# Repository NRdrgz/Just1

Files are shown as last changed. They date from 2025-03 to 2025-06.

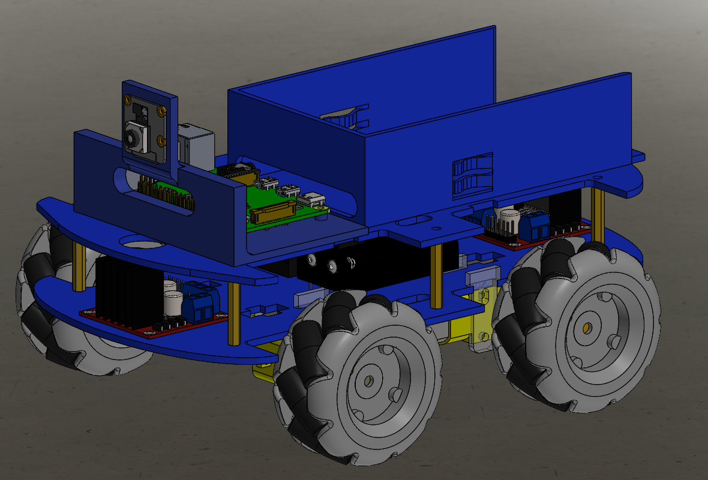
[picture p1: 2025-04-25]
Bot/Hardware/Just1Model.png

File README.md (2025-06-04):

# Just1 - An Open-Source Mecanum Wheel Robot

Just1 is an open-source robotics platform designed for learning, experimentation, and fun! Built around a Raspberry Pi and equipped with mecanum wheels, this robot offers both manual control and autonomous navigation capabilities.

## Project Goals

Just1 was created with several objectives in mind:
- Provide a fun and engaging robotics platform
- Develop practical robotics and programming skills
- Share knowledge and encourage others to build their own robots
- Create an accessible platform for learning and experimentation

## Workspace Organization

### Hardware
Located in `/Bot/Hardware`:
- Bill of Materials (BoM)
- SolidWorks design files
- Assembly instructions and wiring diagrams

### Software
Located in `/Bot/Software`:
- ROS2 packages
- Installation guides
- Manual control documentation

## Current Features

- Complete hardware design with BoM and SolidWorks files
- Comprehensive software documentation for Raspberry Pi setup
- Manual control using Nintendo Controller
- Real-time camera feed accessible via homemade web interface or through Foxglove

## Features in Progress

- Autonomous navigation using ROS2 VSLAM (RTAB Map)
- Add documentation on Camera feedback through websocket

## Short-term To-Do List

- Create detailed README for Hardware folder
- Add assembly and wiring documentation
- Add control and camera feedback on phone
- Use Foxglove CompressedVideo instead of CompressedImage for Camera feedback

## Long-term Goals and Potential Improvements

- Add a Docker Image for easier and faster deployment
- Perform Navigation through Neural Network architecture instead of VSLAM 
- Replace AA batteries with voltage booster for simplified power management
- Integrate LIDAR system, IMU and/or wheel encoders for advanced navigation and experimentation
- Integrate memory / latency profilers to optimize processes and detect memory leaks

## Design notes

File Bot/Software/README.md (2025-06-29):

# Just1 Software

This is a ROS2-based control system for a four-wheeled robot with joystick control.

## References for external ROS packages
- Camera ROS: https://index.ros.org/p/camera_ros/
- Foxglove Bridge: https://github.com/foxglove/ros-foxglove-bridge
- RTAB-Map: https://github.com/introlab/rtabmap_ros

## Installation

1. Install Ubuntu Server 24.04 on your Pi <br>
See `Reads/How_to_Install_Ubuntu_on_Pi.md` <br>
Once you are connected through SSH to your Pi, continue: <br>

2. Install ROS2 on your Pi <br>
See `Reads/How_to_Install_ROS2_on_Pi.md` <br>
We are voluntarily not using a virtual environment because it creates issues with the Camera and with ROS2 <br>

3. Install git and clone this repository on your Pi <br>
```bash
sudo apt install git -y
git clone https://github.com/NRdrgz/Just1.git
cd Just1/Bot/Software
```

4. Install Dependencies: <br>
```bash
sudo apt install python3-pip python3-gpiozero python3-pygame libcap-dev ninja-build libyaml-dev python3-yaml python3-ply python3-jinja2 meson libdrm ros-jazzy-foxglove-bridge python3-smbus i2c-tools ros-jazzy-rtabmap-ros ros-jazzy-imu-filter-madgwick ros-jazzy-navigation2 ros-jazzy-nav2-bringup
pip install --break-system-packages -r requirements.txt
```
5. Build libcamera from source <br>
As libcamera is not available on Ubuntu Server 24.04 we need to install it from the source
```bash
cd ~
git clone https://git.libcamera.org/libcamera/libcamera.git
cd libcamera
meson setup build
sudo ninja -C build install
```
Add the directory to Python search path
```bash
echo 'export PYTHONPATH=/usr/local/lib/aarch64-linux-gnu/python3.12/site-packages:$PYTHONPATH' >> ~/.bashrc
source ~/.bashrc
```

And we also have to build from source pykms
```bash
cd ~
git clone https://github.com/tomba/kmsxx.git
cd kmsxx
meson setup build
sudo ninja -C build install
```
```bash
echo 'export LD_LIBRARY_PATH=/usr/local/lib/aarch64-linux-gnu:$LD_LIBRARY_PATH' >> ~/.bashrc
source ~/.bashrc
```

6. Connect a Nintendo Lic Pro Controller if you have one <br>
See `Reads/How_to_Connect_Nintendo_Pro_Controller.md` <br>

7. Build the ROS2 packages: <br>
```bash
cd ~/Just1/Bot/Software
colcon build --symlink-install
```

To build a single package you can do <br>
```bash
colcon build --packages-select <package_name> --symlink-install
```

8. Source the workspace: <br>
```bash
source install/setup.bash
```

## Usage in Manual
At this point you can control the robot manually. <br>
To start the manual control system: <br>

```bash
ros2 launch just1_bringup just1.launch.py mode:=manual
```

## Get the Video feed
To see the video captured from the Camera, you can either
- Use Foxglove (preferred) <br>
The foxglove_bridge_node used in just1_bringup is used to select the relevant topics to whitelist to Foxglove <br>
You can then visualize Camera data in a Foxglove UI <br>

- Use the homemade websocket:
Activate the camera_web_socket node in just1.launch.py <br>
Navigate to the Web page in src/just1_camera/web/Webpage.html <br>
Make sure to change the PI ip address in the Webpage <br>

## Continue installation for Autonomous mode

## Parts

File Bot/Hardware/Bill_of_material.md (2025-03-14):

# Bill of Material

This are the components used to build Junior.

| Item | Description | Link (as of March 2025) | Total Price (as of March 2025) | Why |
| --- | --- | --- | --- | --- |
| Control Unit | Raspberry Pi v4 8Gb | [Link](https://www.adafruit.com/product/4564?src=raspberrypi) | $83 | 8Gb to have enough memory for AI vision. The Raspberry Pi v5 is great by 5A power supply is hard to find |
| Micro SD card | 16GB Micro SD Card | [Link](https://www.amazon.com/Micro-Adapter-Memory-Tablet-Camera/dp/B0DBLWVSM8) | $7 | Used to install OS on the Pi |
| Wheels + Motors | 4 x 60mm Mecanum Wheels + 4 TT Motors | [Link](https://www.amazon.com/DWWTKL-Mecanum-Omnidirectional-Educational-Accessory/dp/B0CBJJM1KQ) | $16 | Great combo of wheels and TT motors with proper adapters to connect the wheels and motors |
| Motor Drivers | 2 x L298N | [Link](https://www.amazon.com/Controller-H-Bridge-Stepper-Control-Mega2560/dp/B0DPPWFZ1C) | $14 | Cheap with Mosfet but good enough |
| Sensors | Camera Module 3 | [Link](https://www.adafruit.com/product/5657?src=raspberrypi) | $25 |  |
| Pi Power Unit | Power bank for Raspberry Pi | [Link](https://www.amazon.com/Portable-36800mAh-Tri-Outport-External-Compatible/dp/B0936GZ7H3) | $25 | Power bank has a 5V 3A USB C output good for Pi |
| Motors Power Unit | 6 AA batteries holder for motors  | [Link](https://www.amazon.com/LAMPVPATH-Battery-Holder-Bundle-Arduino/dp/B07BNN9PDF) | $7 | Provide 9V to the Motor Drivers |
| Chassis | See 3D models |  | $0 if you find a Robotic club |  |
| **Total** |  |  | **$177** |  |

Here are a bunch of useful screws and wires.
| Item | Link (as of March 2025) | Total Price (as of March 2025) | Why |
| --- | --- | --- | --- |
| Female Female Jumper Wires | [Link](https://www.amazon.com/dp/B09FP5PW45?ref=ppx_yo2ov_dt_b_fed_asin_title&th=1) | $7 | Connect Pi to Motor Driver | 
| Various 2.5 Screws | [Link](https://www.amazon.com/dp/B0CRRCYZHS?ref=ppx_yo2ov_dt_b_fed_asin_title&th=1) | $10 | Screw Pi or Motor drivers | 
| Hex Pylons | [Link](https://www.amazon.com/dp/B01EYQ1TGE?ref=ppx_yo2ov_dt_b_fed_asin_title&th=1) | $10 | Separate both layers of 3D model |

You`ll also need standard wires, soldering iron.

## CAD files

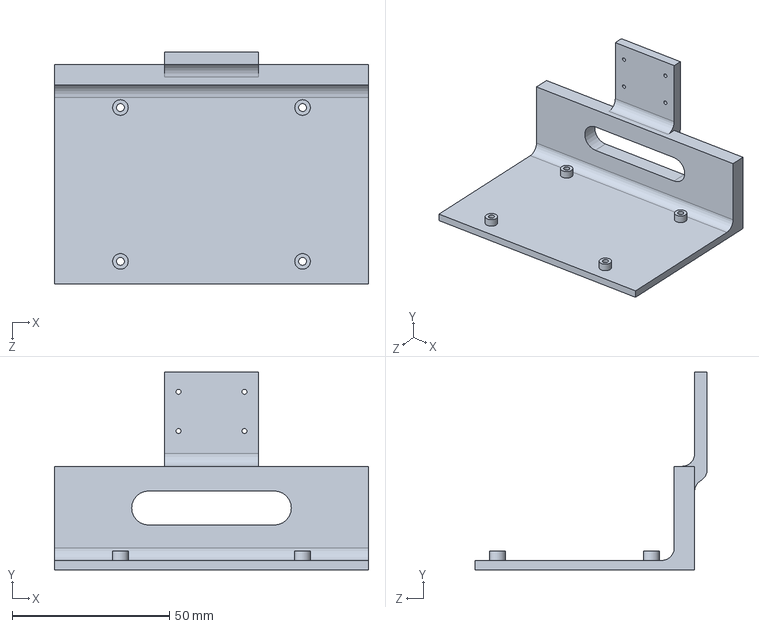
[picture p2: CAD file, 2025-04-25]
Bot/Hardware/Solidworks/Parts/Raspberry Holder.SLDPRT
100.0 x 63.0 x 74.0 mm

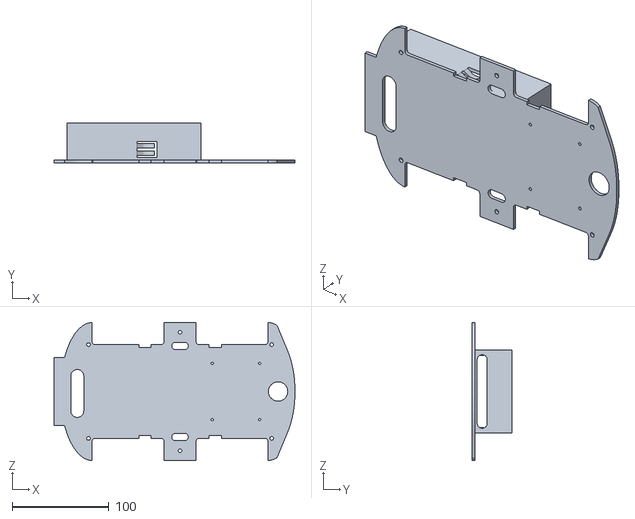
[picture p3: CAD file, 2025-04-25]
Bot/Hardware/Solidworks/ToPrint/Car chassis - top.STL
248.8 x 40.8 x 142.5

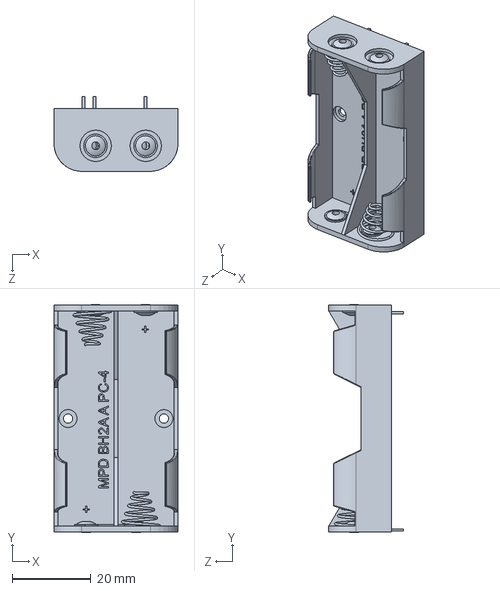
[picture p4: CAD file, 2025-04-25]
Bot/Hardware/Solidworks/Parts/2x AA Battery Pack.SLDPRT
31.5 x 58.0 x 19.0 mm

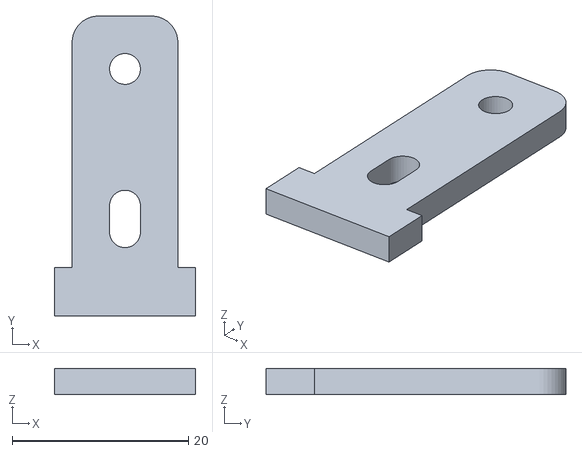
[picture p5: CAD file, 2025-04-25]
Bot/Hardware/Solidworks/ToPrint/Holder Motor.STL
16.0 x 34.0 x 3.00

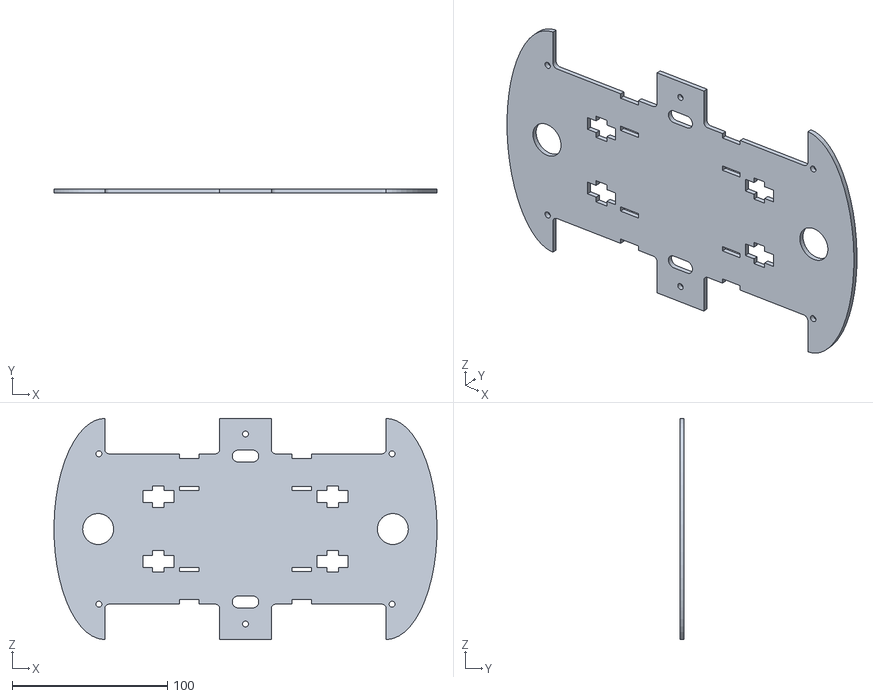
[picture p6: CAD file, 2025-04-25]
Bot/Hardware/Solidworks/ToPrint/Car chassis bottom.STL
247.0 x 2.85 x 142.5

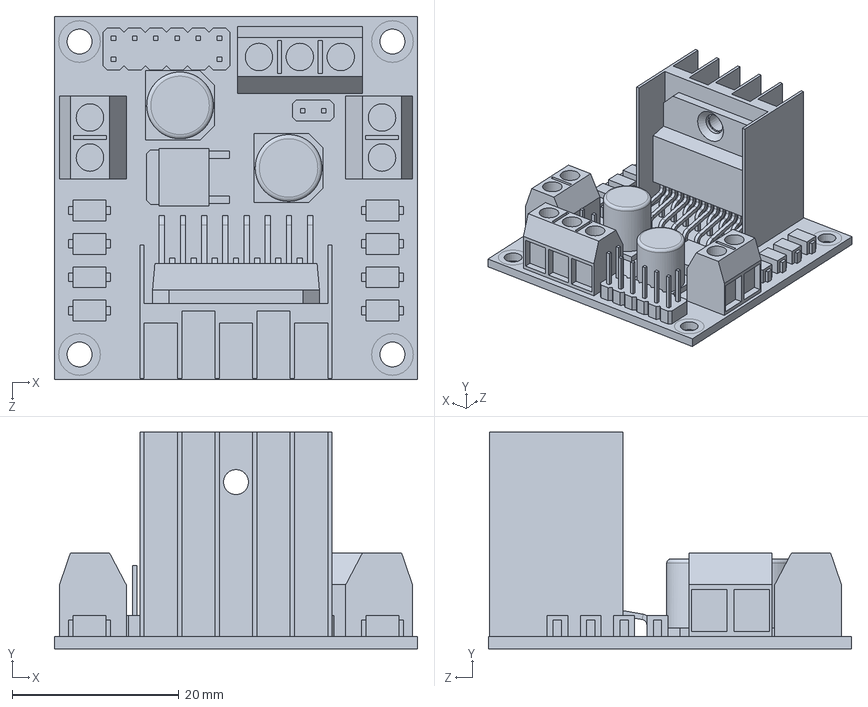
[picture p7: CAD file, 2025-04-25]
Bot/Hardware/Solidworks/Parts/L298N.SLDPRT
43.5 x 26.0 x 43.5 mm

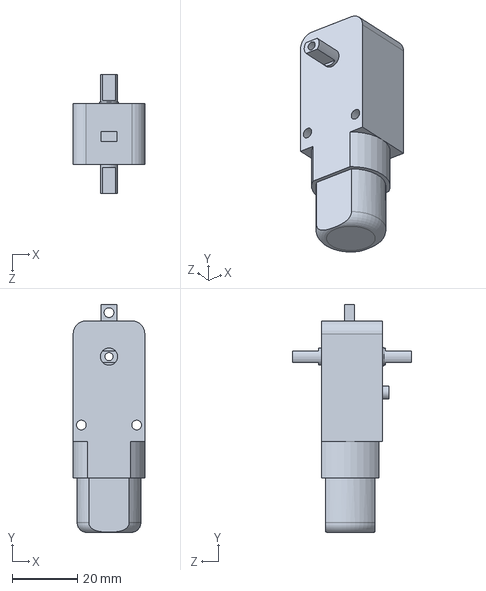
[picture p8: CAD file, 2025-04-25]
Bot/Hardware/Solidworks/Parts/TT motor.SLDPRT
22.0 x 70.0 x 36.6 mm

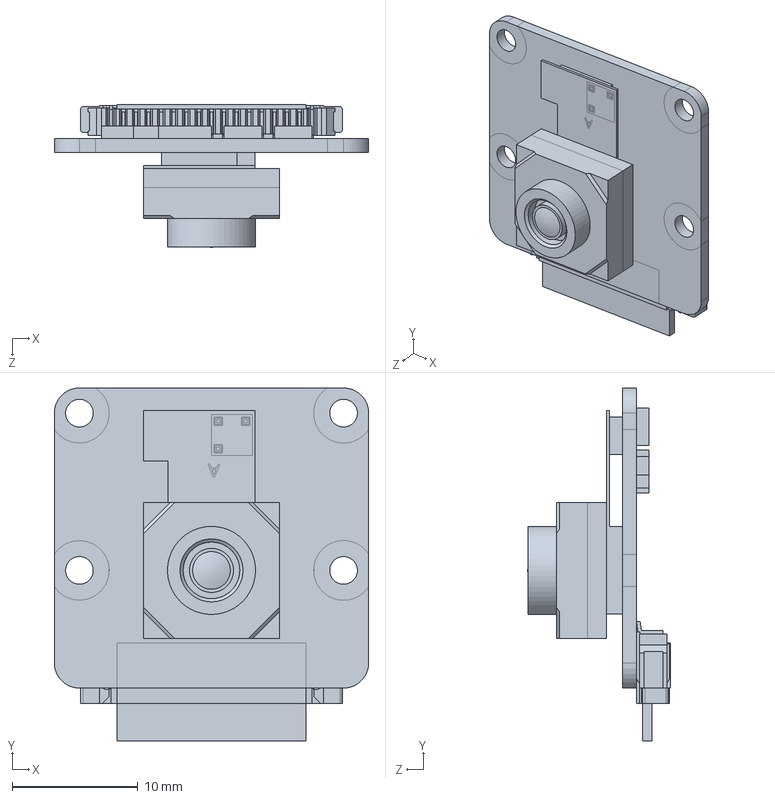
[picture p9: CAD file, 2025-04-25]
Bot/Hardware/Solidworks/Parts/Camera Moudule 3 v8.SLDPRT
25.0 x 28.1 x 11.3 mm

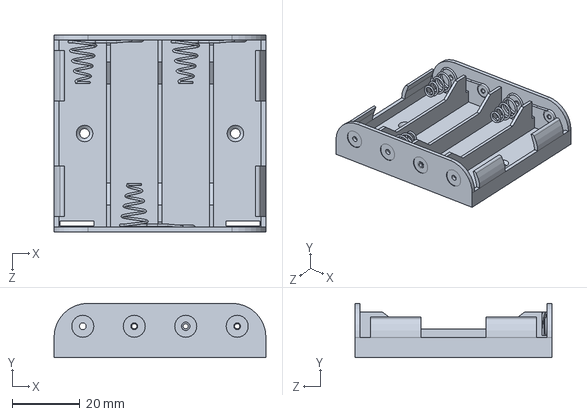
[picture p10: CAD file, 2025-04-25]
Bot/Hardware/Solidworks/Parts/4x AA Battery Pack.SLDPRT
62.4 x 16.0 x 58.0 mm

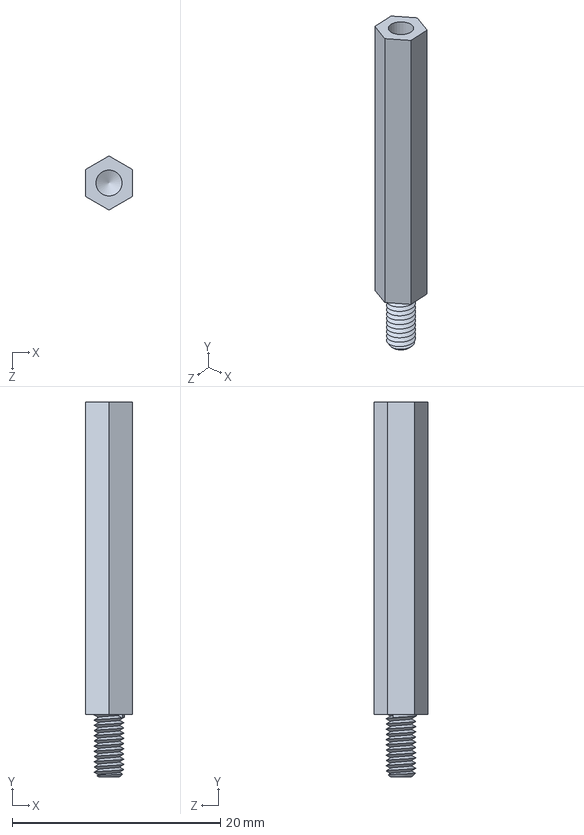
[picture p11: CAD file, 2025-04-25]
Bot/Hardware/Solidworks/Parts/Pillar Hex.SLDPRT
4.50 x 36.0 x 5.20 mm

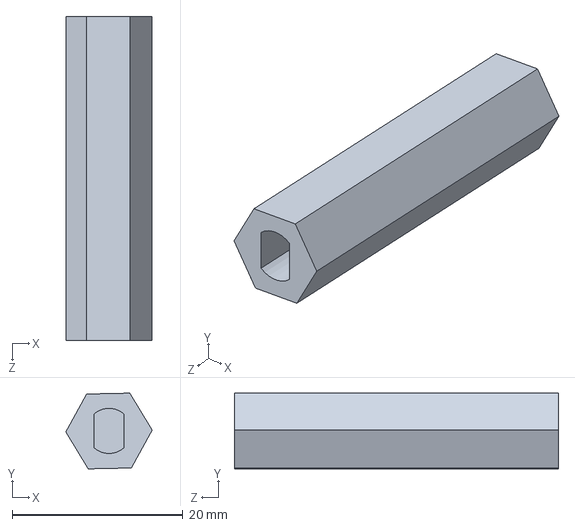
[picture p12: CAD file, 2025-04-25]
Bot/Hardware/Solidworks/Parts/Coupling Adapter.SLDPRT
10.1 x 8.89 x 38.0 mm

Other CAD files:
Bot/Hardware/Solidworks/Parts/Holder Motor.SLDPRT
Bot/Hardware/Solidworks/ToPrint/Raspberry Holder.STL
Bot/Hardware/Solidworks/Parts/Car chassis - top.SLDPRT
Bot/Hardware/Solidworks/Parts/Car chassis bottom.SLDPRT

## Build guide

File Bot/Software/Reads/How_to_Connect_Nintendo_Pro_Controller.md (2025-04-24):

# Connect to the Nintendo Lic Pro Controller
To connect to the Lic Pro Controller from the Raspberry Pi <br>
First make sure Pi has bluetooth enabled <br>
```bash
sudo apt install bluetooth bluez bluez-tools rfkill -y
sudo systemctl enable bluetooth
sudo systemctl start bluetooth
```

Put controller in pairing mode  <br>
Then <br>
```bash
bluetoothctl
power on
agent on
default-agent
scan on
```

You'll see something like  <br>
[NEW] Device XX:XX:XX:XX:XX:XX Lic Pro Controller <br>

```bash
pair XX:XX:XX:XX:XX:XX
trust XX:XX:XX:XX:XX:XX
connect XX:XX:XX:XX:XX:XX
```

Then <br>
```bash
exit
```

You can verify if it worked by using joystick <br>
```bash
sudo apt install joystick
jstest /dev/input/js0
```

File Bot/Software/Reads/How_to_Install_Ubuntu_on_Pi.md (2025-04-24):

# Install Ubuntu on Raspberry Pi 
## Step 1: Download Ubuntu Image

1. Go to the [Ubuntu Raspberry Pi page](https://ubuntu.com/raspberry-pi).
2. Download your preferred version (e.g., Ubuntu Server 24.04 LTS). Make sure to install Ubuntu Server instead of Ubuntu Desktop if you want to avoid plugging keyboard and mouse on the Pi.

---

## Step 2: Flash the Image to microSD

1. Download and install the [Raspberry Pi Imager](https://www.raspberrypi.com/software/).
2. Launch the Imager and:
   - **Choose OS**: Select “Other general-purpose OS > Ubuntu”
   - **Choose Storage**: Select your microSD card
   - **Customize before writing**:
     - You should have a popup offering you to input custom settings
     - Enable **Set hostname** (e.g., `raspberrypi.local`). This will allow to connect to it without IP address
     - Enable and set **SSH** (e.g., username `your-username`, password `your-password`)
     - Enable and configure **Wi-Fi**:
       - SSID: `your-network-name`
       - Password: `your-password`
       - Wi-Fi country: `US` (or your 2-letter country code)

3. Click **Save**, then **Write** to flash the image.

---

## Step 3: First Boot

1. Insert the microSD into your Raspberry Pi.
2. Power it on.

The Pi will:
- Automatically connect to the Wi-Fi
- Enable SSH access
- Be ready for headless setup

Wait for 5-10 min for the installation to complete

---

## Step 4: Connect via SSH

Once the Pi is online, open a terminal on your computer and connect using:

```bash
ssh your-username@raspberrypi
```

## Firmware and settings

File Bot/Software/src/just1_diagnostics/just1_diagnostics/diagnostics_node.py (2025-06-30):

import rclpy
from rclpy.node import Node
import time
from just1_motors.utils_motors import (
    setup,
    stop_all,
    test_wheel,
    cleanup,
    control_wheel,
)
from sensor_msgs.msg import Joy


class DiagnosticsNode(Node):
    def __init__(self):
        super().__init__("diagnostics_node")
        self.get_logger().info("Diagnostics Node initialized")

        # Declare parameters
        self.declare_parameter("test_wheel", "")
        self.declare_parameter("test_movement", "")
        self.declare_parameter("test_joystick", False)
        self.declare_parameter("speed", 50)

        # Initialize GPIO and motors
        setup()

        # Create subscriber for joystick
        self.joystick_subscriber = self.create_subscription(
            Joy, "joy", self.joystick_callback, 10
        )
        self.joystick_data = None

        # Run diagnostics based on parameters
        self.run_diagnostics()

    def joystick_callback(self, msg):
        """Callback for joystick messages"""
        self.joystick_data = msg

    def run_diagnostics(self):
        """Run diagnostics based on parameters"""
        test_wheel = self.get_parameter("test_wheel").get_parameter_value().string_value
        test_movement = (
            self.get_parameter("test_movement").get_parameter_value().string_value
        )
        test_joystick = (
            self.get_parameter("test_joystick").get_parameter_value().bool_value
        )
        speed = self.get_parameter("speed").get_parameter_value().integer_value

        if test_wheel:
            self.test_wheel(test_wheel)
            self.cleanup_and_shutdown()
        elif test_movement:
            self.test_movement(test_movement, speed)
            self.cleanup_and_shutdown()
        elif test_joystick:
            self.test_joystick()
        else:
            self.get_logger().error("No valid test option specified")
            self.cleanup_and_shutdown()

    def cleanup_and_shutdown(self):
        """Cleanup and shutdown the node"""
        cleanup()
        self.get_logger().info("Diagnostics completed")
        rclpy.shutdown()

    def test_joystick(self):
        """Display joystick values"""
        print("\nJoystick Test Mode")
        print("Press Ctrl+C to exit")
        print("Waiting for joystick data...")

        # Create a timer to periodically check joystick data
        self.timer = self.create_timer(0.1, self.print_joystick_data)

    def print_joystick_data(self):
        """Print joystick data periodically"""
        if self.joystick_data is not None:
            print("\n" + "=" * 50)
            print("Joystick Data:")
            print(f"Axes: {[f'{x:.2f}' for x in self.joystick_data.axes]}")
            print(f"Buttons: {self.joystick_data.buttons}")
            print("=" * 50)

    def test_wheel(self, wheel_name):
        """Test a specific wheel"""
        self.get_logger().info(f"Testing {wheel_name} wheel")
        test_wheel(wheel_name)
        time.sleep(2)
        stop_all()

    def test_movement(self, movement_name, speed):
        """Test a specific movement"""
        self.get_logger().info(f"Testing {movement_name} movement at speed {speed}")

        movement_map = {
            "forward": self.move_forward,
            "backward": self.move_backward,
            "left": self.move_left,
            "right": self.move_right,
            "spin_clockwise": self.spin_clockwise,
            "spin_counterclockwise": self.spin_counterclockwise,
            "diagonal_forward_right": self.move_diagonal_forward_right,
            "diagonal_forward_left": self.move_diagonal_forward_left,
            "diagonal_backward_right": self.move_diagonal_backward_right,
            "diagonal_backward_left": self.move_diagonal_backward_left,
            "curve_right": self.move_curve_to_right,
            "curve_left": self.move_curve_to_left,
            "lateral_arc": self.move_lateral_arc,
            "square": self.do_square,
        }

        if movement_name in movement_map:
            movement_map[movement_name](speed)
            time.sleep(10)
            stop_all()
        else:
            self.get_logger().error(f"Invalid movement name: {movement_name}")

    # Movement functions
    def move_forward(self, speed):
        control_wheel("front_left", speed)
        control_wheel("front_right", speed)
        control_wheel("back_left", speed)
        control_wheel("back_right", speed)

    def move_backward(self, speed):
        control_wheel("front_left", -speed)
        control_wheel("front_right", -speed)
        control_wheel("back_left", -speed)
        control_wheel("back_right", -speed)

    def move_left(self, speed):
        control_wheel("front_left", -speed)
        control_wheel("front_right", speed)
        control_wheel("back_left", speed)
        control_wheel("back_right", -speed)

    def move_right(self, speed):
        control_wheel("front_left", speed)
        control_wheel("front_right", -speed)
        control_wheel("back_left", -speed)
        control_wheel("back_right", speed)

    def spin_clockwise(self, speed):
        control_wheel("front_left", speed)
        control_wheel("front_right", -speed)
        control_wheel("back_left", speed)
        control_wheel("back_right", -speed)

    def spin_counterclockwise(self, speed):
        control_wheel("front_left", -speed)
        control_wheel("front_right", speed)
        control_wheel("back_left", -speed)
        control_wheel("back_right", speed)

    def move_diagonal_forward_right(self, speed):
        control_wheel("front_left", speed)
        control_wheel("front_right", 0)
        control_wheel("back_left", 0)
        control_wheel("back_right", speed)

    def move_diagonal_forward_left(self, speed):
        control_wheel("front_left", 0)
        control_wheel("front_right", speed)
        control_wheel("back_left", speed)
        control_wheel("back_right", 0)

    def move_diagonal_backward_right(self, speed):
        control_wheel("front_left", 0)
        control_wheel("front_right", -speed)
        control_wheel("back_left", -speed)
        control_wheel("back_right", 0)

    def move_diagonal_backward_left(self, speed):
        control_wheel("front_left", -speed)
        control_wheel("front_right", 0)
        control_wheel("back_left", 0)
        control_wheel("back_right", -speed)

    def move_curve_to_right(self, speed):
        control_wheel("front_left", speed * 1.2)
        control_wheel("front_right", speed)
        control_wheel("back_left", speed * 1.2)
        control_wheel("back_right", speed)

    def move_curve_to_left(self, speed):
        control_wheel("front_left", speed)
        control_wheel("front_right", speed * 1.2)
        control_wheel("back_left", speed)
        control_wheel("back_right", speed * 1.2)

    def move_lateral_arc(self, speed):
        control_wheel("front_left", speed)
        control_wheel("front_right", -speed)
        control_wheel("back_left", 0)
        control_wheel("back_right", 0)

    def do_square(self, speed):
        movements = [
            (self.move_forward, 2),
            (stop_all, 1),
            (self.move_right, 2),
            (stop_all, 1),
            (self.move_backward, 2),
            (stop_all, 1),
            (self.move_left, 2),
            (stop_all, 1),
        ]

        for movement, duration in movements:
            movement(speed)
            time.sleep(duration)
            stop_all()
            time.sleep(0.5)


def main(args=None):
    rclpy.init(args=args)
    node = DiagnosticsNode()

    try:
        rclpy.spin(node)
    except KeyboardInterrupt:
        pass
    finally:
        node.destroy_node()


if __name__ == "__main__":
    main()

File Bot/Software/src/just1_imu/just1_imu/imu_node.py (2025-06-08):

import rclpy
from rclpy.node import Node
from sensor_msgs.msg import Imu
import smbus
import math
import time
from typing import Dict, Tuple


class MPU6050Error(Exception):
    """Custom exception for MPU6050 related errors."""

    pass


class MPU6050Publisher(Node):
    """
    ROS2 node for publishing MPU6050 IMU data.

    This node reads data from the MPU6050 IMU sensor and publishes it as ROS2 Imu messages.
    It includes calibration, error handling, and configurable parameters.
    """

    # MPU6050 registers and addresses
    DEVICE_ADDRESS = 0x68
    PWR_MGMT_1 = 0x6B
    ACCEL_XOUT_H = 0x3B
    GYRO_CONFIG = 0x1B
    ACCEL_CONFIG = 0x1C

    def __init__(self):
        super().__init__("mpu6050_publisher")

        # Declare parameters
        self.declare_parameter("i2c_bus", 1)
        self.declare_parameter("publish_rate", 10.0)
        self.declare_parameter("calibration_samples", 100)
        self.declare_parameter("gyro_range", 250)  # in degrees/s
        self.declare_parameter("accel_range", 2)  # in g

        # Get parameters
        self.i2c_bus = self.get_parameter("i2c_bus").value
        self.publish_rate = self.get_parameter("publish_rate").value
        self.calibration_samples = self.get_parameter("calibration_samples").value

        # Initialize I2C bus
        try:
            self.bus = smbus.SMBus(self.i2c_bus)
        except Exception as e:
            self.get_logger().error(f"Failed to initialize I2C bus: {str(e)}")
            raise MPU6050Error("I2C bus initialization failed")

        # Initialize sensor
        self._initialize_sensor()

        # Calibration offsets
        self.accel_offsets = (0.0, 0.0, 0.0)
        self.gyro_offsets = (0.0, 0.0, 0.0)

        # Perform calibration
        self._calibrate_sensor()

        # Create publisher
        self.publisher_ = self.create_publisher(Imu, "imu/data_raw", 10)

        # Create timer
        self.timer = self.create_timer(1.0 / self.publish_rate, self.timer_callback)

        self.get_logger().info("MPU6050 publisher node initialized successfully")

    def _initialize_sensor(self):
        """Initialize the MPU6050 sensor with proper configuration."""
        try:
            # Wake up the MPU6050
            self.bus.write_byte_data(self.DEVICE_ADDRESS, self.PWR_MGMT_1, 0)

            # Configure gyroscope range
            gyro_range = self.get_parameter("gyro_range").value
            gyro_config = {250: 0x00, 500: 0x08, 1000: 0x10, 2000: 0x18}.get(
                gyro_range, 0x00
            )
            self.bus.write_byte_data(self.DEVICE_ADDRESS, self.GYRO_CONFIG, gyro_config)

            # Configure accelerometer range
            accel_range = self.get_parameter("accel_range").value
            accel_config = {2: 0x00, 4: 0x08, 8: 0x10, 16: 0x18}.get(accel_range, 0x00)
            self.bus.write_byte_data(
                self.DEVICE_ADDRESS, self.ACCEL_CONFIG, accel_config
            )

        except Exception as e:
            self.get_logger().error(f"Failed to initialize MPU6050: {str(e)}")
            raise MPU6050Error("Sensor initialization failed")

    def _calibrate_sensor(self):
        """Calibrate the sensor by collecting offset values."""
        self.get_logger().info("Starting sensor calibration...")

        accel_sum = [0.0, 0.0, 0.0]
        gyro_sum = [0.0, 0.0, 0.0]

        for _ in range(self.calibration_samples):
            data = self._read_sensor_data()
            accel_sum = [a + b for a, b in zip(accel_sum, data["accel"])]
            gyro_sum = [a + b for a, b in zip(gyro_sum, data["gyro"])]
            time.sleep(0.01)  # Small delay between readings

        # Calculate average offsets
        self.accel_offsets = tuple(-x / self.calibration_samples for x in accel_sum)
        self.gyro_offsets = tuple(-x / self.calibration_samples for x in gyro_sum)

        self.get_logger().info("Sensor calibration completed")

    def _apply_deadzone(self, value: float, threshold: float = 0.06) -> float:
        """Apply a deadzone to the value.
        This is to prevent the robot from moving when the IMU is not moving.
        """
        return 0.0 if abs(value) < threshold else value

    def _read_word(self, register: int) -> int:
        """
        Read a word from the MPU6050.

        We can only read one byte at a time and MPU6050 writes data with 2 bytes.
        So we need to read the high and low bytes separately.
        The value is stored in two's complement format, so we need to convert it properly.
        """
        try:
            # Read the high byte (most significant byte)
            high = self.bus.read_byte_data(self.DEVICE_ADDRESS, register)
            # Read the low byte (least significant byte)
            low = self.bus.read_byte_data(self.DEVICE_ADDRESS, register + 1)
            # Shift the high byte 8 bits to the left and add the low byte
            value = (high << 8) + low
            # If the value is negative (MSB is 1), we need to convert it from two's complement
            if value >= 0x8000:
                value = -((65535 - value) + 1)
            return value
        except Exception as e:
            self.get_logger().error(f"Failed to read from MPU6050: {str(e)}")
            raise MPU6050Error("Sensor read failed")

    def _read_sensor_data(self) -> Dict[str, Tuple[float, float, float]]:
        """Read raw sensor data."""
        try:
            accel_x = self._read_word(self.ACCEL_XOUT_H)
            accel_y = self._read_word(self.ACCEL_XOUT_H + 2)
            accel_z = self._read_word(self.ACCEL_XOUT_H + 4)
            gyro_x = self._read_word(self.ACCEL_XOUT_H + 8)
            gyro_y = self._read_word(self.ACCEL_XOUT_H + 10)
            gyro_z = self._read_word(self.ACCEL_XOUT_H + 12)

            return {
                "accel": (accel_x, accel_y, accel_z),
                "gyro": (gyro_x, gyro_y, gyro_z),
            }
        except Exception as e:
            self.get_logger().error(f"Failed to read sensor data: {str(e)}")
            raise MPU6050Error("Sensor data read failed")

    def timer_callback(self):
        """Timer callback to read and publish IMU data."""
        try:
            # Get the IMU data
            data = self._read_sensor_data()
            accel_x, accel_y, accel_z = data["accel"]
            gyro_x, gyro_y, gyro_z = data["gyro"]

            # Apply calibration offsets
            # We do not offset the z-axis in order to keep the gravity acceleration
            accel_x += self.accel_offsets[0]
            accel_y += self.accel_offsets[1]

            gyro_x += self.gyro_offsets[0]
            gyro_y += self.gyro_offsets[1]
            gyro_z += self.gyro_offsets[2]

            # Convert raw accelerometer values to m/s²
            accel_scale = 9.80665 / 16384.0
            # Convert raw gyro values to rad/s
            gyro_scale = math.pi / (180.0 * 131.0)
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

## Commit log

2025-03-14 Add BoM
2025-04-05 Add test_motor
    Add test motor to test the configuration
2025-04-07 Add test motor and test movements file
    Add test motor file testing the proper wiring
    test movements file to test the mecanum wheels movement
    test controller to test the input of the Lic pro controller
2025-04-16 Update pwm cycle
2025-04-16 Update utils motors
2025-04-16 Enable pwm
2025-04-16 Update motor control in ROS2
2025-04-17 Move Python files in correct folders
    [controller_node.py]
2025-04-17 Change wheelspeed msg def
2025-04-17 Share just wheel msg
2025-04-17 Rename wheel speeds
2025-04-18 Move WheelSpeeds to a separate interface
2025-04-18 Convert wheel speed to float
2025-04-18 Fix wheel going bad direction
    [controller_node.py]
2025-04-18 Fix wheel speed
2025-04-18 Revert "Fix wheel speed"
    This reverts commit 6154c4763e41cfa64c431336aabb51056d44aabb.
    [controller_node.py]
2025-04-21 Revert "Fix diagnostic menu"
    This reverts commit 1e087d79fbaf1a76683bc54f5cba4e6c93c81111.
    [diagnostics_node.py]
2025-04-21 Change sleep to ROS2 timer
2025-04-23 Add just1 camera
2025-04-23 Add web socket node
2025-04-23 Remove state monitor and fix web socket name
    [camera_web_socket.py]
2025-04-23 Fix name camera web socket
2025-04-23 Fix websocket
    Resize the image and convert to bytes
    [camera_web_socket.py]
2025-04-23 Add state monitor and remove web socket
2025-04-23 Add back web socket and remove state monitor
2025-04-23 Fix camera ratio
2025-04-23 Correct convert to BGR
    [camera_node.py]
2025-04-24 Add test camera python
2025-04-25 Add back camera to the bringup
2025-04-25 Remove print from camera
2025-04-25 Fix issue with self
    [camera_web_socket.py]
2025-04-25 Wrap send frames
2025-04-25 Remove path from serve frame
2025-04-25 Improve image
    Flip image
    Convert to RGB
    Increase to 60 FPS
    [camera_node.py, camera_web_socket.py]
2025-04-25 Put back camera in manual mode
2025-04-25 Add Solidworks elements
    [2x AA Battery Pack.SLDPRT, 4x AA Battery Pack.SLDPRT, Camera Moudule 3 v8.SLDPRT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]
2025-04-25 Remove camera test
2025-04-25 Fix some bugs
    Fix joystick audio issue
    Fix manual control import
    Flip camera horizontally as well
    [camera_node.py, manual_controller_node.py]
2025-04-25 Try optimization of camera system
2025-04-25 Fix shutdown of motor and websocket
    [camera_web_socket.py, manual_controller_node.py]
2025-04-25 Fix shutdown web socket
    [camera_web_socket.py]
2025-04-25 Fix again web server shutdown
    [camera_web_socket.py]
2025-04-25 Resimplify web socket
    Went too far trying to shutdown graciously
2025-05-09 only send joystic and wheelspeeds
2025-05-09 Add back camera image
2025-05-09 Add camera encoder node
2025-05-09 Add message encoder initialized
2025-05-09 Add action camera encoder
2025-05-09 Add SPS in every frame
2025-05-09 Fix encoder
2025-05-09 Rework encoder
2025-05-09 Make sure we have a full frame
2025-05-09 Add debug message error
    [camera_encoder_node.py]
2025-05-09 Encode in separate thread
2025-05-09 Try to encode one frame at a time
2025-05-09 Send exactly one frame
2025-05-09 Catch errors for debugging
    [camera_encoder_node.py]
2025-05-09 Remove the one frame reader
2025-05-09 Print frame for debug
2025-05-09 Fix packet to data
    [camera_encoder_node.py]
2025-05-09 Print debug string
2025-05-09 print frame
2025-05-09 Detect frame messages
2025-05-09 print chunk and frame
2025-05-09 Force each frame to be keyframe
2025-05-09 Remove test on frame beginning
2025-05-09 Log frame data
2025-05-09 Reset nal unit data
    [camera_encoder_node.py]
2025-05-11 Replace homemade camera node by camera_ros
    [camera_encoder_node.py, camera_node.py, camera_web_socket.py]
2025-05-11 Get back to homemade camera node for better control
2025-05-11 Fix shutdown encoder
2025-05-15 Put back img flip
    [camera_node.py]
2025-05-27 Python to test imu
2025-06-04 Add IMU to bringup and remove camera flip
    [camera_node.py]
2025-06-04 Improve IMU node
2025-06-04 Update imu topic in bringup
2025-06-04 Add Lidar driver
2025-06-04 Whitelist lidar ld19 topic
2025-06-06 Add rotation to Lidar TF
2025-06-06 Fix yaw pitch roll order
2025-06-06 Add RTAB Map ICP Odometry
2025-06-06 Remove wait for imu
2025-06-06 Add IMU filter from madgwick
2025-06-06 Add tf for base link to base imu
2025-06-06 Remap IMU
2025-06-06 Fix IMU tf and increase wait for transform
2025-06-06 Add wait imu to icp odom
2025-06-06 Reverse imu remapping
2025-06-06 Rename imu link
2025-06-06 Increase imu publish rate
2025-06-07 Put back IMU at 10Hz
2025-06-07 Put IMU at 15 Hz
2025-06-07 Sync IMU and Scan
2025-06-07 Revert "Sync IMU and Scan"
    This reverts commit 06f724c7fc35bb0677b3975ee815d4d5e0348dc8.
    [imu_node.py, scan_imu_sync.py]
2025-06-07 Try with IMU at 12 Hz
2025-06-07 Try IMU at 60 Hz
2025-06-07 Try IMU at 10.5 Hz
2025-06-07 Try updating lidar driver for better timestamp
2025-06-07 Revert "Try updating lidar driver for better timestamp"
    This reverts commit b70f7e8d998c0dcefa87415bb079e1a6a24d3dd6.
    [imu_node.py]
2025-06-07 Sync scan and imu
2025-06-07 Remove wait imu to init
2025-06-07 Try zeta on IMU filtering
2025-06-07 Fix scan imu sync
    [scan_imu_sync.py]
2025-06-07 Fix sync scan imu
    [scan_imu_sync.py]
2025-06-07 Try a deadzone on the IMU data
2025-06-08 Keep gravity in calibration
2025-06-08 Correct imu link tf
2025-06-29 Print nav2 params
2025-06-29 Fix keepout filter
2025-06-29 Remove keepout and speed filter from params
2025-06-30 Add comment for all parameters + change velocity params
2025-06-30 Add percentage above 0 to avoid division by 0
    [autonomous_controller_node.py]
2025-06-30 Avoid division by 0
    [autonomous_controller_node.py]
2025-07-01 Add a minimum percentage for autonomous wheel speed
2025-07-01 Fix autonomous motor controller
    [autonomous_controller_node.py]
2025-07-01 Remove footprint
2025-07-01 Revert "Simplify autonomous controller"
    This reverts commit 118681eda5bbaab79b2cdd0df567fa78d9432be1.
    [autonomous_controller_node.py]
2025-07-01 Revert "Simplify autonomous controller"
    This reverts commit 74b4ec4647a1f9db0fb1d4f728749d30fa49baef.
    [autonomous_controller_node.py]
2025-07-01 Revert "Fix autonomous controller"
    This reverts commit 297f843681e125aec1572397115bf33109a10fdc.
    [autonomous_controller_node.py]
2025-07-03 Normalize wheel speed before publishing
2025-07-03 Fix float in wheel speed
    [autonomous_controller_node.py]
